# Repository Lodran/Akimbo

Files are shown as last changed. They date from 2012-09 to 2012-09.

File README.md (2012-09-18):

RepRap Mendel Akimbo

Copyright 2012 by Ron Aldrich.

Licensed under GNU GPL v2

======

Akimbo is a re-imagining of the Mendel frame, designed to address specific goals.

  1) Improve the frame's clearance, particularly for the X carriage and extruders, with particular focus on dual-extruder clearance.
  
  2) Make the frame easier to assemble correctly.
  
  3) Make the frame more rigid.
  
  Akimbo differs from other designs in several important ways, in order to address those goals.
  
  1) The top horizontal rods are further apart than the original Sells and Prusa designs; This allows an extruder to utilize the space between the motors, increasing build height.
  
  2) The top of the frame is tilted outward; This improves clearance for the X axis, by insuring that the A frame is outside of most of the moving parts, when the Z axis is at it's uppermost range.
  
  3) The Z linear rod mounts are connected to bottom rod of the A frame, improving frame rigidity, and ease of assembly.
  
  4) The Y linear rod mounts recall the older (Sells) design, which insures that the spacing between the Y linear rods and the frame horizontal rods is consistent, making it easier to align the print bed.
  
  5) The X ends are inverted, with the X linear rods mounted at the top of the X end, rather than at the bottom; This allows the X linear rods to move higher than they otherwise would be able to.
  
  6) On all 3 axis, one side is fully constrained (using LM8UU bearings, or equivalent bushings), and one side is constrained only against rotation, using a pair of roller bearings; This prevents mis-aligned, or slightly bent Linear rods from causing the axis to bind.
  
  7) The design supports dual extruders, each with its own carriage, and X axis motor; This allows differences between hot-end length on the two extruders to easily be adjusted for in software, and allows one carriage to be parked offsides while the other is in use (no drooling all over the print in progress).

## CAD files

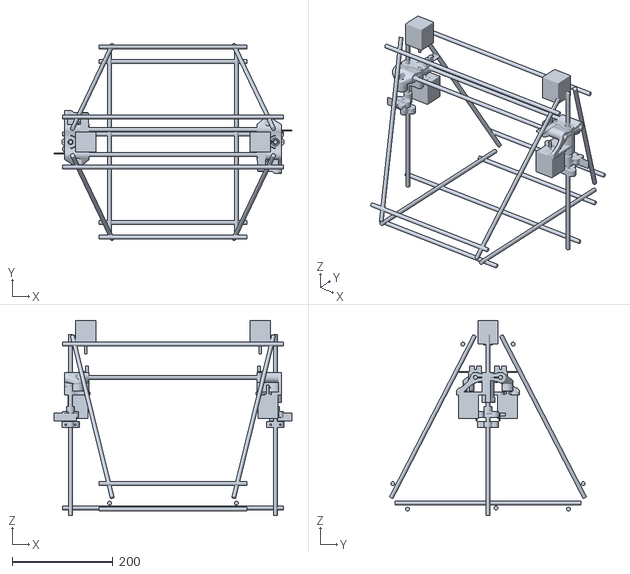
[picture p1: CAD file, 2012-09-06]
assembly.stl
473.0 x 391.5 x 387.7

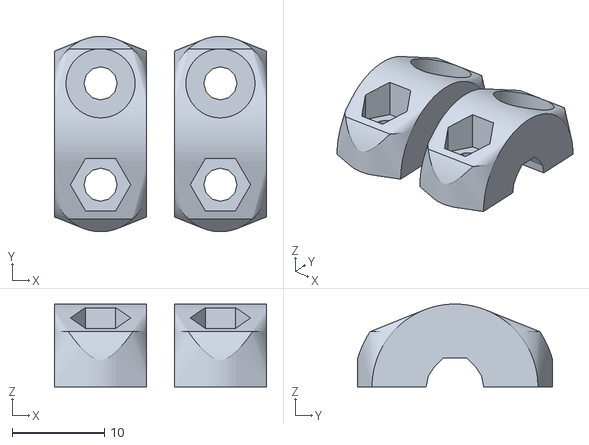
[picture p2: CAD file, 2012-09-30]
Parts/z_motor_coupler@_4.stl
23.0 x 21.2 x 9.00

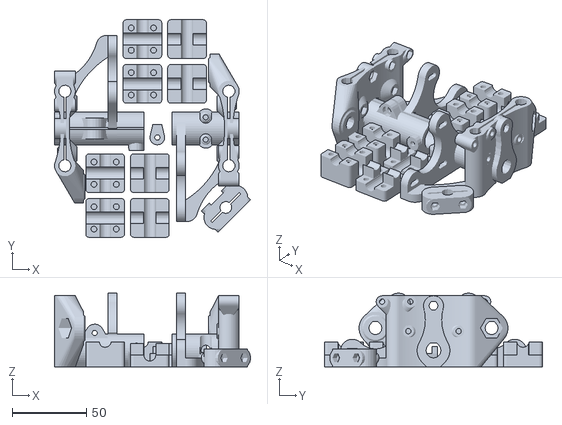
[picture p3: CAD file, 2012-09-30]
Plates/plate_3.stl
131.6 x 146.0 x 49.5

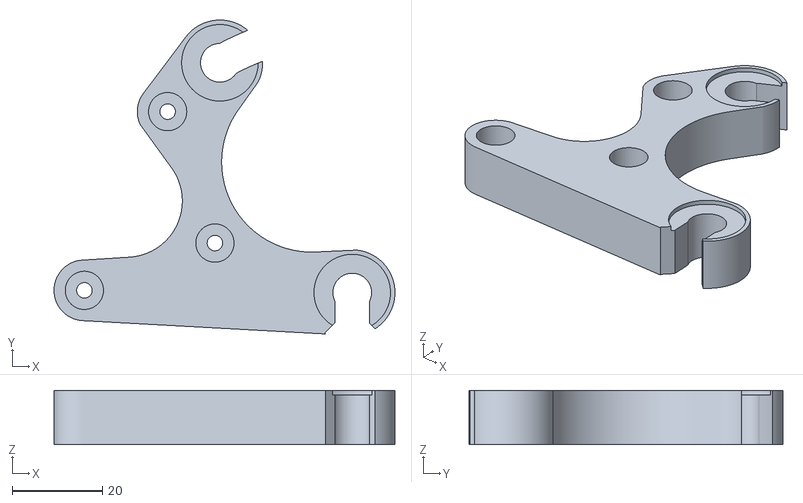
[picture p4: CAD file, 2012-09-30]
Parts/y_motor_bracket@_1.stl
75.8 x 69.7 x 12.0

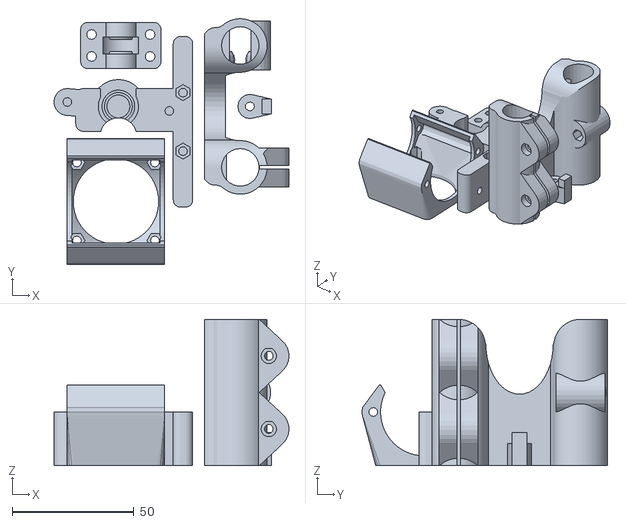
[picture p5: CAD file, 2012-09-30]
Plates/plate_5.stl
96.4 x 100.7 x 60.0

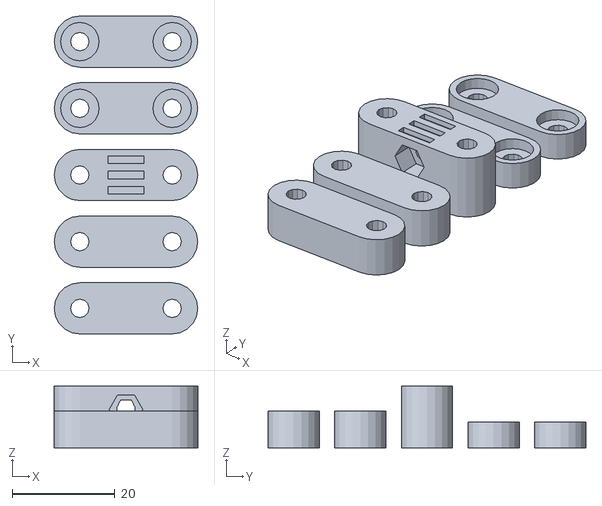
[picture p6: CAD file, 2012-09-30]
Parts/y_axis_belt_clamp@_1.stl
28.0 x 62.0 x 12.0

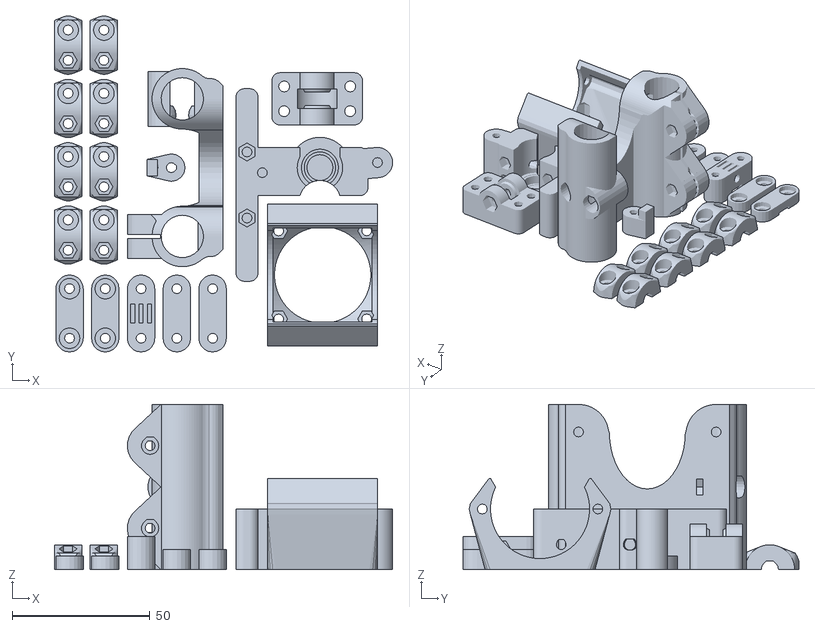
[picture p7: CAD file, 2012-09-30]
Plates/plate_4.stl
122.9 x 122.1 x 60.0

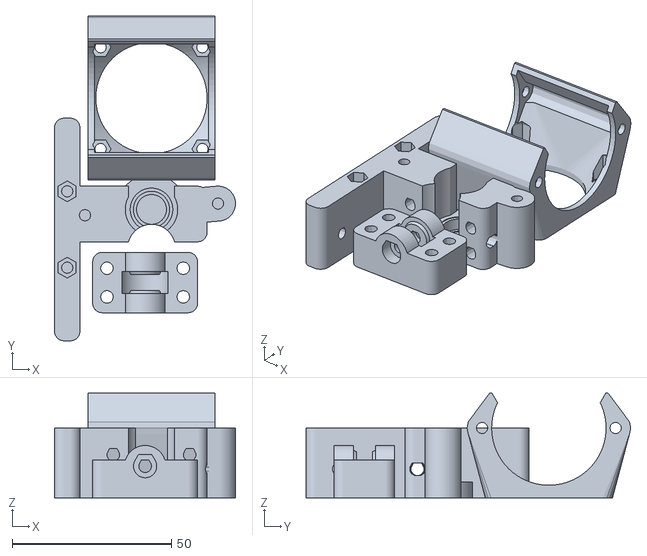
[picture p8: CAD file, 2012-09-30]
Parts/akimbo_extruder_@_1.stl
56.9 x 102.1 x 33.0

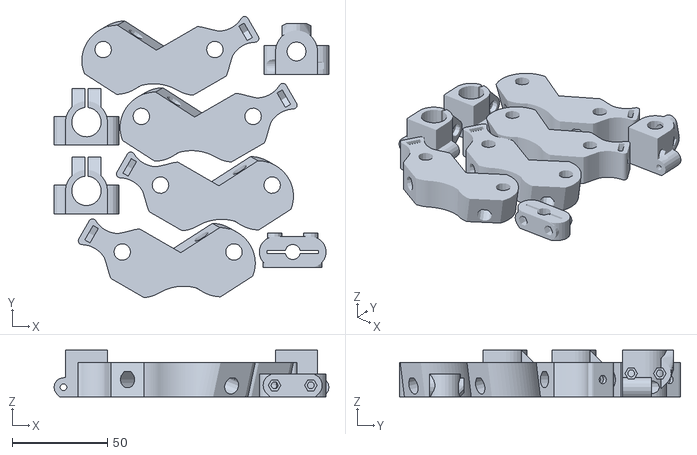
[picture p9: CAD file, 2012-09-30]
Plates/plate_1.stl
144.0 x 147.2 x 24.4

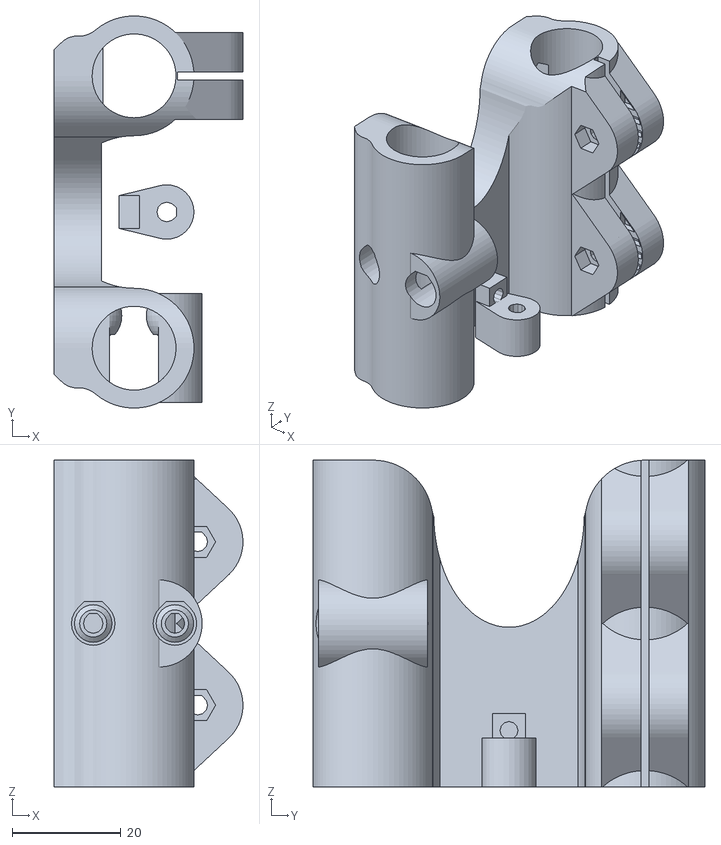
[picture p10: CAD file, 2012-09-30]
Parts/akimbo_carriage_@_2.stl
34.7 x 72.0 x 60.0

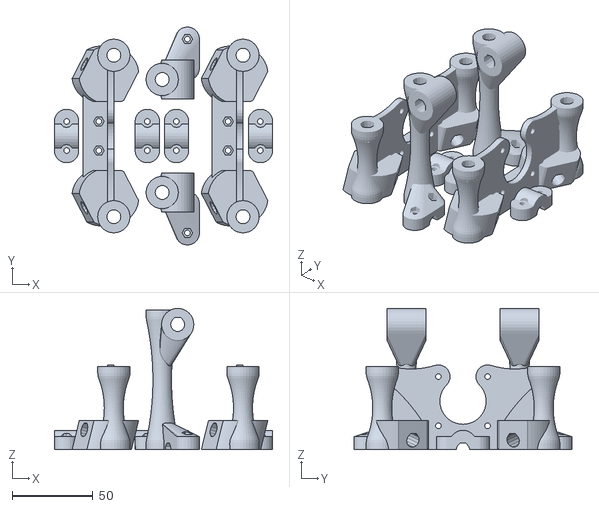
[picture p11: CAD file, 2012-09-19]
Plates/frame_plate_2.stl
135.0 x 135.0 x 87.5

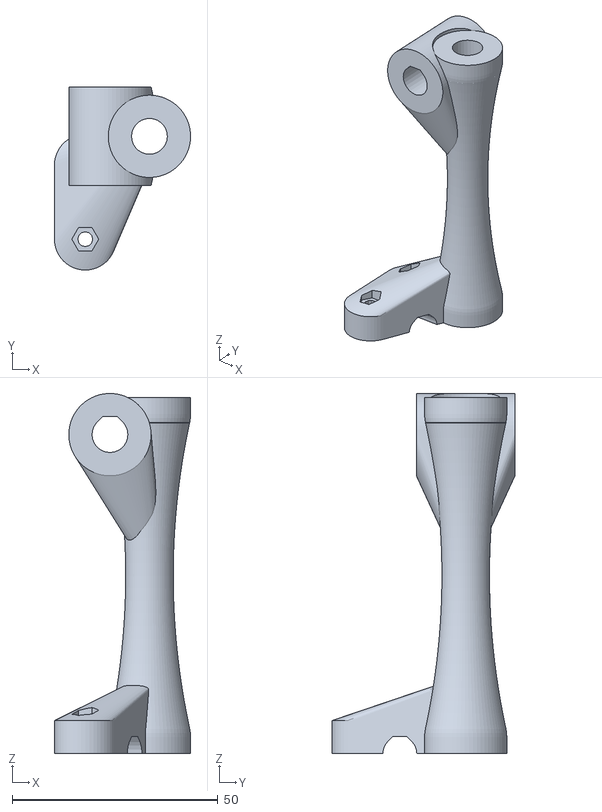
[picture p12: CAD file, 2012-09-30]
Parts/z_bottom_frame_clamp_mirrored_@_1.stl
33.1 x 44.5 x 87.5

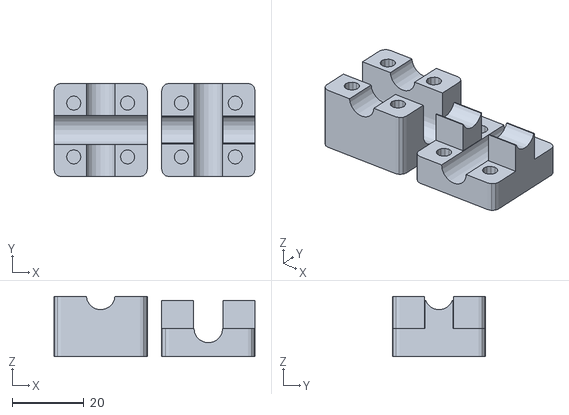
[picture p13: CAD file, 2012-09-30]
Parts/akimbo_barclamp_@_4.stl
56.0 x 26.0 x 16.9

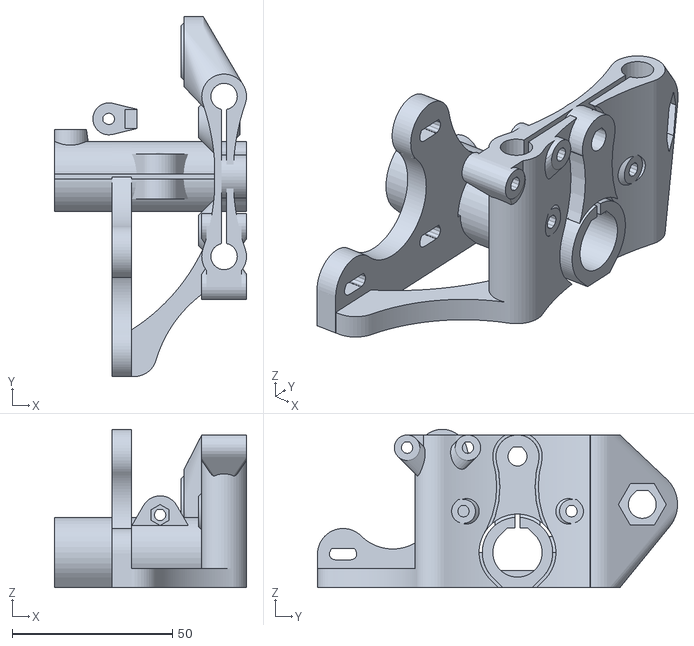
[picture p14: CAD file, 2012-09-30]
Parts/akimbo_x_end_right_@_1.stl
60.0 x 112.5 x 49.5

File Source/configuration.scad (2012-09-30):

//
// RepRap Mendel Akimbo
//
// A Mendel variant, which improves the frame's clearance and stability
//  by increasing its triangulation.
//
// Copyright 2012 by Ron Aldrich.
//
// Licensed under GNU GPL v2
//
//	configuration.scad
//
//	General configuration settings.
//
//	Because this file is intended to be somewhat interchangable with 
//		configuration.scad from prusajr's github repository, there is 
//		more configuration in "moreConfiguration.scad".
//
//  Only the metric variant is tested. Other variants are not supported, and will most likely
//    create unworkable parts.
//
//	Edit layer_height to be greater than the height of one printed layer, 
//		but less than the height of two printed layers.
//


metric = 0;	// All parts are metric - use both M3 and M4 bolts.
sae = 1;		// All parts are SAE - use only #6/32 bolts.
m3only = 2;	// All parts are metric, but use only M3 bolts.
hybrid = 3;	// Mix of metric and SAE - use M3 and 6/32 bolts.

variant = metric;

layer_height = .25;

nut_slop = .2;		// I aim for a "interference fit" for nuts - a bit of force required to place the nut.

bolt_slop = .6;	// The aim here is to just barely allow the bolt to fit through the hole, without having to thread it in.

_actual_m3_diameter = 3+bolt_slop;
_actual_m4_diameter = 4+bolt_slop;
_actual_6_32_diameter = 3.4+bolt_slop;

_actual_m3_nut_diameter = 5.5/cos(30)+nut_slop;
_actual_m4_nut_diameter = 6.87/cos(30)+nut_slop;
_actual_m5_nut_diameter = 7.85/cos(30)+nut_slop;
_actual_6_32_nut_diameter = 7.85/cos(30)+nut_slop;

_m3_diameters = [_actual_m3_diameter, _actual_6_32_diameter, _actual_m3_diameter, _actual_m3_diameter];
_m3_nut_diameters = [_actual_m3_nut_diameter, _actual_6_32_nut_diameter, _actual_m3_nut_diameter, _actual_m3_nut_diameter];

_m4_diameters = [_actual_m4_diameter, _actual_6_32_diameter, _actual_m3_diameter, _actual_6_32_diameter];
_m4_nut_diameters = [_actual_m4_nut_diameter, _actual_6_32_nut_diameter, _actual_m3_nut_diameter, _actual_6_32_nut_diameter];

m3_diameter = _m3_diameters[variant];
m3_nut_diameter = _m3_nut_diameters[variant];

m4_diameter = _m4_diameters[variant];
m4_nut_diameter = _m4_nut_diameters[variant];

m5_diameter = 5+bolt_slop;
m5_nut_diameter = _actual_m5_nut_diameter;
m5_bolt_head_height = 4;

m6_diameter = 6+bolt_slop;
m6_nut_diameter = 10/cos(30)+nut_slop;
m6_bolt_head_height = 4;

m8_diameter = 8;

m8_nut_diameter = 12.8/cos(30)+nut_slop;
m8_nut_thickness = 7.7;
m8_bolt_head_height = 6;
m8_half_nut_height = 3.85;

threaded_rod_diameter = 8.7;

actual_smooth_rod_diameter = 8;
smooth_rod_diameter = actual_smooth_rod_diameter+.25;

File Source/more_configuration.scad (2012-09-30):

//
// RepRap Mendel Akimbo
//
// A Mendel variant, which improves the frame's clearance and stability
//  by increasing its triangulation.
//
// Copyright 2012 by Ron Aldrich.
//
// Licensed under GNU GPL v2
//
// moreConfiguration.scad
//
//	General configuration settings that didn't exist in prusajr's configuration.scad
//
//	These settings are here, rather than in configuration.scad, in
//		order to keep configuration.scad interchangable with prusajr.s version.
//
// Edit extrusion_width to be greater than the width of one shell, but less than the width of two shells.

include <configuration.scad>

extrusion_width = .6;

vertical_slop = .6;
horizontal_slop = .3;

_actual_m3_nut_thickness = 2.5;
_actual_m4_nut_thickness = 3.5;
_actual_6_32_nut_thickness = 3.25;

_m3_nut_thickness = [_actual_m3_nut_thickness, _actual_6_32_nut_thickness, _actual_m3_nut_thickness, _actual_m3_nut_thickness];

_m4_nut_thickness = [_actual_m4_nut_thickness, _actual_6_32_nut_thickness, _actual_m3_nut_thickness, _actual_6_32_nut_thickness];

m3_nut_thickness = _m3_nut_thickness[variant];
m3_washer_diameter = 7.5;

m4_nut_thickness = _m4_nut_thickness[variant];

m3_bolt_head_height = 3;
m3_bolt_head_diameter = 6+horizontal_slop;

m4_bolt_head_height = 4;
m4_bolt_head_diameter = 7+horizontal_slop;

// Don't edit things after here.

x = 0;
y = 1;
z = 2;

bearing_length = 0;
bearing_body_diameter = 1;
bearing_flange_diameter = 2;
bearing_flange_width = 3;
bearing_rod_diameter = 4;

// linear_roller_bearing = [2, 6, 6, 0, 3];

683_bearing = [3, 7, 7, 0, 3];
683_bearing_clearance = [0.4, 0.4, 0.4, 0, 2];

623_bearing = [4, 10, 10, 0, 6];
623_bearing_clearance = [0.4, 0.4, 0.4, 0, 2];

624_bearing = [5, 13, 13, 0, 4];
624_bearing_clearance = [0.4, 0.4, 0.4, 0, 2];

608_bearing = [7, 22, 22, 0, 8];
608_bearing_clearance = [0.4, 0.4, 0.4, 0, 2];

115_bearing = [4, 11, 11, 0, 5];
115_bearing_clearance = [0.4, 0.4, 0.4, 0, 3];

106_bearing = [3, 10, 10, 0, 6];
106_bearing_clearance = [0.4, 0.4, 0.4, 0, 0];

126_bearing = [4, 12, 12, 0, 6];
126_bearing_clearance = [0.4, 0.4, 0.4, 0, 3];

128_bearing = [3.5, 12, 12, 0, 8];
128_bearing_clearance = [0.4, 0.4, 0.4, 4];

lm8uu = [24, 15, 15, 0, 8];
lm8uu_clearance = [0.4, 0.4, 0.4, 0, 0];

igus = [10, 10, 15, 1, 8];
igus_clearance = [0.4, 0.4, 0.4, 0.4, 0];

part_color_1 = [1, .9, 0];
part_color_2 = [.9, 1, 0];

wood_color_1 = [111/256, 78/256, 55/256];
wood_color_2 = wood_color_1+[.2, .2, .2];
wood_color_3 = wood_color_1-[.2, .2, .2];

nema17_hole_spacing = 1.25*25.4;

ramps_size = [102, 60];

ramps_mounts = [[-35.76, -20.86],
                [-35.76, 27.4],
                [39.17, 27.4],
                [45.52, -20.86]];

//echo(ramps_mounts);

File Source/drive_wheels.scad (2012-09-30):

//
// RepRap Mendel Akimbo
//
// A Mendel variant, which improves the frame's clearance and stability
//  by increasing its triangulation.
//
// Copyright 2012 by Ron Aldrich.
//
// Licensed under GNU GPL v2
//
// drive_wheels.scad
//
// Size and shape definitions for various extruder drive wheels, for direct drive extruders.
//

drive_wheel_length = 0;
drive_wheel_radius = 1;
drive_wheel_hob_radius = 2;
drive_wheel_hob_center = 3;

makerbot_mk7 = [
	11,
	12.5/2,
	10.65/2,
	7.45
];

arcol_11x5 = [
	13,
	11/2,
	9.1/2,
	13-5
];

arcol_8x5 = [
	13,
	8/2,
	6.1/2,
	13-5
];

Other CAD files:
Parts/akimbo_extruder_mirrored_@_1.stl
Parts/z_bottom_frame_clamp_@_1.stl
Parts/y_pillow_block_@_1.stl
Parts/akimbo_x_end_left_@_1.stl
Source/motor.scad
Parts/akimbo_endstop_mount_@_2.stl
Parts/bottom_vertex@_2.stl
Parts/bottom_vertex_@_2.stl
Parts/bottom_vertex_mirrored@_2.stl
Parts/bottom_vertex_mirrored_@_2.stl
Parts/top_vertex_@_2.stl
Parts/y_roller_bearing_block.stl
Parts/z_bottom_frame_clamp@_1.stl
Parts/z_bottom_frame_clamp_mirrored@_1.stl
Parts/z_linear_rod_clamp_@_4.stl
Source/akimbo_barclamp.scad
Source/akimbo_carriage.scad
Source/akimbo_endstop_mount.scad
Source/akimbo_extruder.scad
Source/akimbo_x_end.scad
Source/assembly.scad
Source/barbell.scad
Source/bottom_vertex.scad
Source/dimensions.scad
Source/extruder_fan_shroud.scad
Source/frame_computations.scad
Source/frame_plate.scad
Source/functions.scad
Source/optical_endstop.scad
Source/pill.scad
Source/teardrops.scad
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

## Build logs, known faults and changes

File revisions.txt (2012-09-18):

Version 0.1

Initial development release.

Version 0.2

  top_vertex.scad
    Fixed Z motor mount bolt holes.
    Removed a lot of plastic.
  
  bottom_vertex.scad
    Removed a lot of plastic.

  z_bottom_frame_clamp.scad
    Fixed conflict between Z linear rod bottom frame rod.
    Removed a lot of plastic.
  
  z_linear_rod_clamp.scad
    New with this release.

Version 0.3

  top_vertex.scad
    Increased the diameter of the horizontal bracket, to make measurement easier.

  z_bottom_frame_clamp.scad
    Increased the angle of the overhang on the frame end of the bracket, to make it print nicer.
    Increased the diameter of the ends of the bracket, to make measurement easier.

  z_linear_rod_clamp.scad
    Increased the thickness of the base of the rod clamp.
    Tweaked the geometry to side-step manifold errors.

  Plates.zip
    Added frame_plate_1.stl

Version 0.4

  Added X and Y axis parts.
  
    top_vertex.scad
      Eliminated the inside section, which was only there to make jigging the frame easier.
      Improved the dogbone profile of the horizontal rod clamps.
    
    z_bottom_frame_clamp.scad
      Improved the dogbone profile of the horizontal rod clamps.

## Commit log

2012-08-13 Version 0.1
    [assembly.scad, barbell.scad, bottom_vertex.scad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]
2012-08-13 Added automation for building the .stl and .zip files.
    [assembly.scad, bottom_vertex.scad, bottom_vertex@_2.stl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]
2012-08-13 More automation
    [assembly.stl]
2012-08-15 Version 0.2
    [assembly.scad, assembly.stl, bottom_vertex.scad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]
2012-08-17 Version 0.3
    [assembly.stl, bottom_vertex@_2.stl, bottom_vertex_mirrored@_2.stl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]
2012-09-04 Version 0.4 - X and Z axis.
    [akimbo_carriage.scad, akimbo_extruder.scad, akimbo_x_end.scad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]
2012-09-06 Version 0.4 - More X axis work
    [akimbo_carriage.scad, akimbo_carriage_@_2.stl, akimbo_extruder.scad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]
2012-09-10 Version 0.4
    [akimbo_carriage.scad, akimbo_carriage_@_2.stl, akimbo_extruder.scad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]
2012-09-18 Rearranged plate 2 to fit a 150x150 build area.
    [frame_plate.scad]
2012-09-18 Rearranged plate 1 so that it fits in a 150mm square.
    [frame_plate.scad]
2012-09-18 renamed akimbo_z_endstop_mount to akimbo_endstop_mount, as this mount is used on the Y axis as well.
    [akimbo_endstop_mount.scad]
2012-09-18 renamed akimbo_z_endstop_mount.scad to akimbo_endstop_mount.scad
    [akimbo_x_end.scad]
2012-09-18 move object to z=0, when print_orientation == true
    [y_pillow_block.scad]
2012-09-18 Version 0.4, first commit.
    [y_axis_plate.scad]
2012-09-19 Fixed rendering issues that occur when compiled from x_axis_plate.scad.
    [akimbo_x_end.scad]
2012-09-19 Added the Z endstop mount.
    [x_axis_plate.scad]
2012-09-19 Show annotations
    [akimbo_extruder.scad]
2012-09-19 Eliminate vertical rotation - it looks better angled.
    [extruder_fan_shroud.scad]
2012-09-19 Add the Y axis endstop flag mount.
    [y_pillow_block.scad]
2012-09-19 Correct Z Leadscrew length
    [dimensions.scad]
2012-09-19 Prep work for adding bar clamps to assembly.scad
    [akimbo_barclamp.scad]
2012-09-19 Fix idler bracket, tweak things.
    [akimbo_extruder.scad]
2012-09-19 include configuration.scad and dimensions.scad, to insure that $fa and $fs are set properly.
    [barbell.scad]
2012-09-19 Add option for print_orientation
    [extruder_fan_shroud.scad]
2012-09-19 Fix print orientation.
    [extruder_fan_shroud.scad]
2012-09-19 Add fan shrouds to extruder plate.
    [x_axis_plate.scad]
2012-09-19 Version 0.4.1
    [akimbo_barclamp_@_4.stl, akimbo_carriage_@_2.stl, akimbo_endstop_mount_@_2.stl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]
2012-09-19 Idler tweaks.
    [akimbo_extruder.scad]
2012-09-19 Added a patch to thicken the plastic between the motor and the idler bracket, so that slic3r will have enough room for 2 extrusions - the single wall breaks too easily.
    [akimbo_extruder.scad]
2012-09-19 Beefed up the idler bracket, made it more printable.
    [akimbo_extruder.scad]
2012-09-20 Fixed the idler hinge void
    [akimbo_extruder.scad]
2012-09-20 Fixed idler bracket, removed hash (#) colors.
    [akimbo_extruder.scad]
2012-09-22 Added vitamin descriptions.
    [akimbo_carriage.scad]
2012-09-25 Add "vitiamin" output.
    [akimbo_extruder.scad]
2012-09-25 Switched back to 624 bearing for the idler clamp, as it appears to make for a more reliable extruder.
    [akimbo_extruder.scad]
2012-09-25 Fixed bugs having to do with rendering both X Ends on a single plate.
    [akimbo_x_end.scad]
2012-09-25 Added "Vitamin" documentation.
    [akimbo_endstop_mount.scad]
2012-09-25 Added "Vitamin" documentation, Added non-print orientation.
    [akimbo_barclamp.scad]
2012-09-25 Hack to insure that release quality models are generated.
    [barbell.scad]
2012-09-25 Changed X and Y linear rod lengths to match Prusa i2 exactly (400mm rods will still work).
    [dimensions.scad]
2012-09-25 Added computations needed for positioning the Y axis linear rods.
    [frame_computations.scad]
2012-09-25 Added definitions for more vitamins.
    [vitamin.scad]
2012-09-25 First commit.
    [z_motor_coupler.scad]
2012-09-25 By default, make a single (2 part) coupler, not a plate.
    [z_motor_coupler.scad]
2012-09-25 Add Y axis parts, and Z motor couplers.
    [assembly.scad]
2012-09-26 Version 0.5
    [akimbo_carriage_@_2.stl, akimbo_extruder_@_1.stl, akimbo_extruder_mirrored_@_1.stl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]
2012-09-30 Once more, with feeling.
    [akimbo_barclamp.scad, akimbo_carriage.scad, akimbo_endstop_mount.scad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]
